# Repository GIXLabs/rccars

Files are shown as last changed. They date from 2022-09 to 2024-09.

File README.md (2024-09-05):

# Purpose

The following tutorial will get you up and running to build an RC car with the provided materials. All of the soldering is already done and the most of the code is flashed onto the brain board. It will be your responsibility to use the tools provided to you in your orientation bag along with the tools available in the Prototyping Lab to design and build a chassis for your car.

### Bill of Materials



# Electronics Assembly

1. Collect the above components from the Prototyping Lab staff.

1. Attach the components to the individual boards. AAA battery pack to brain board (only goes in one way). Bluetooth module to Bluetooth board (RCA, not RCM). Motors to motor board (needs a screwdriver and wires may need to be switched later).

    Component assembly

1. Stack the boards together with the brain at the bottom and Bluetooth at the top. Make sure to align them properly (see image).

    Full assembly

1. Try placing 3 AAA batteries in their holder and turn it on. If you've assembled everything correctly, the blue and red lights on the underside of the Bluetooth module should start blinking.

# Flashing Code

1. The code for the brain board is written in CircuitPython, which means you will not need to download any software to edit and manipulate the code. 
1. Download the RC Car code from [here](src/python/code.py). Make sure it is named `code.py`.

    Image of the button to click

1. Using a micro USB cable, connect the brain board to your computer (you do not need to disconnect the other boards). Your computer should now have a new USB drive available named `CIRCUITPY` where the code is stored.
1. Click and drag `code.py` onto `CIRCUITPY`, replacing the file that is on the drive.
1. Your code should now be running on the brain board. If you would like to edit this code, just open `code.py` in any text editor (TextEdit and NotePad are fine). The new code will run whenever you save.
    1. Editing code this way does not give you access to any debugging outputs, so you may want to edit using [Mu](https://codewith.mu/en/download) or [Thonny](https://thonny.org/) so you can read any `print()` statements you add to the code.
    1. The max speed of the default code is slow, which you may want to change if you want to win the race.
    1. Python uses spacing in a particular way, so you may need to match the indendation of lines.
    1. For more details on how the code works see [here.](src/README.md)

# Connecting via Remote
1. Place the Bluetooth module marked `RCM` in the remote. It should only fit one way.

1. Plug in the 9V batteries on both your remote and turn on the AAA batteries on your car.

1. The lights on the Bluetooth dongles (HC-05) will stop blinking when they have successfully paired.

1. If it fails to pair, try power cycling the car ands the remote.

# Make your Chassis
1. Design and build the body of the RC car, you are welcome to use the materials provided in the Prototyping Lab from cardboard to wood. Make sure it holds everything! We've produced a tutorial if you'd like to start with a lasered template [here](lasering.md).

1. Attach the gear motors to the body of the RC car that you have designed/built and assemble the tires. Depending on how you attach the motors, you may have to change some wires to get it to move forward (instructions below).

# Debugging Motors
If you have been able to connect to your RC car, but it is going the wrong direction, you may need to swap the motor wires.
- If your car is going backward when it should be going forward - Swap the red and black wires on both motors.
- If your car is going left when it should be going right or right when it should be going left - Swap which side of the motor driver your motors are wired to.
- For other problems, ask a member of the Prototyping Lab staff.

### Congratulations you are now connected to the RC car! Happy racing! 🏁🏎

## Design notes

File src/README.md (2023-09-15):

# Theory of Operation
The RC Car consists of two parts:
- The car, which runs on CircuitPython
- The remote, which runs on C

They communicate through two paired Bluetooth dongles (HC-05), with the remote acting as a sender and car acting as a receiver. We expect you will want to edit the car code, but don't recommend editing the remote code.

The remote code first sets up each pin, then goes into an infinite loop. Each time through the loop, the code looks for which button is pressed and sends the corresponding command over the Bluetooth connection. When no button is pressed the remote sends the "stop" command ('S').

The car code first setups up each pin appropriately as either input or output, then goes into an infinite loop. Each time through the loop, the code checks for a command from the remote. When a command is received, a series of `if` and `elif` statements check to see what command was sent and tells the motors what to do accordingly.

The car controls direction via a scheme called tank steering. Instead of having a wheel that turns at the front to determine direction, like in a car, the two wheels move in different directions depending on which way you would like to turn. For example, a right turn involves spinning the left wheel forward and the right wheel backwards. While this allows for a tighter turning radius, it makes smooth turns rather challenging. This steering scheme was chosen for the ease of assembly and simplicity of the code.

# Commands

Image of controller with buttons

| Command | Action |
| --- | ---|
| F | Turn both motors on moving forward. |
| L | Turn left by spinning the right motor forward and the left motor backwards |
| R | Turn right by spinning the left motor forward and the right motor backwards |
| B | Go backwards by spinning both motors backward |
| S | Stop both motors (note: there is no button associated with this on the remote) |
| Q | Currently does nothing, but could be programmed on the car to do whatever you would like |
| N | Boost by turning up the speed to the maximum for 2 seconds. 10 second cooldown |

# Boost
The boost is the most confusing part of the code. It works by first detecting that the 'N' character was sent.
1. Check whether enough time has elapsed since the last boost. Default cooldown is 10 seconds.
    1. Set the motor speed to the maximum value.
        1. Setting the speed impacts all motion of the car. For example, the left and right turns will also go at whatever you most recently set the speed to.
    1. Set the car to move forward and wait for 2 seconds so it moves forward at maximum speed for 2 seconds.
    1. Set the speed back to the default (slower) speed.
    1. Reset the Bluetooth buffer to clear extra commands from the remote that may have come in during the boost (don't delete this, but don't feel like you have to understand it either).
    1. Save the time you last boosted so the cooldown can take effect.

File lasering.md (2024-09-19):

# Important laser rules
1. **DON'T WALK AWAY FROM A RUNNING LASER** - every makerspace eventually burns down due to lasers. We suggest bringing a stool and your computer with you. Unattended cuts will be interrupted and the user may have their access revoked.
1. Only use approved materials - materials already in the Lab are pre-approved, but you will need to check with Prototyping Lab staff if you want to cut or engrave something else.

# Making a basic laser chassis (no design experience needed)

1. Choose from one of the templates made by our staff, downloading the file as an svg.
    1. Formula E by Aayush Kumar (Cohort 7). [SVG here.](/CAD/svg/RC_Car_Formula-E/RC_Car_Formula-E_layout.svg)
    
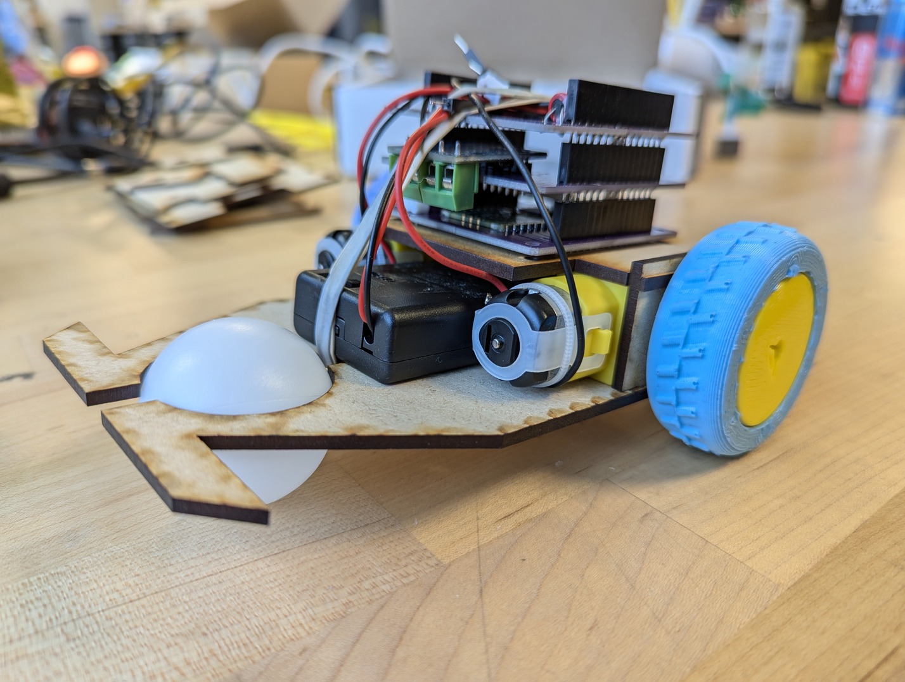
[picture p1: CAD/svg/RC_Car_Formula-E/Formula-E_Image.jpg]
Formula-E car image
    

    1. Van by Liliana Hsu (Cohort 7). [SVG here.](/CAD/svg/RC_Car_Van/RC_Car_Van_layout.svg)
    
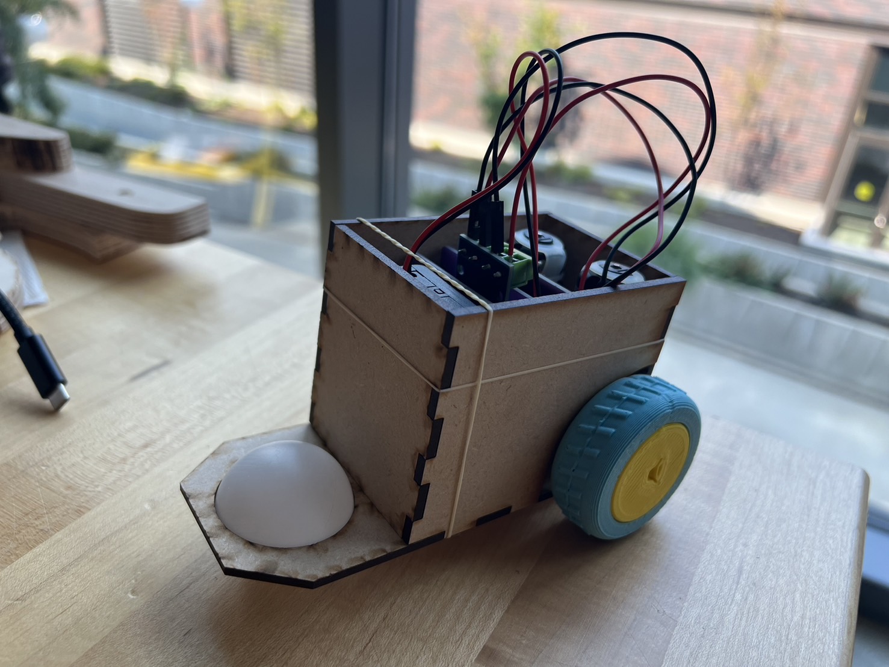
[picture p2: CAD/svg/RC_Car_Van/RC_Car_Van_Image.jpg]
Van car image
    

    1. Batperson car by Kevin Arne. [SVG here.](/CAD/svg/RC_Car_Batperson/base_template.svg)
    
    Batperson car image
1. Ask a member of staff to invite you to the Glowforge system. You will need to sign up for an account, but it is free. Please skip any features that ask for a credit card.
    1. You will get an email and you'll need to click "Click here to get started." Feel free to skip the tutorials.
1. "Create a new design" and "Upload a file" in the [Glowforge interface](https://app.glowforge.com)

    Image of Glowforge home screen

1. Find the 1/8" MDF in the laser material storage and put a sheet of it in your laser on the black honeycomb tray. Position doesn't matter much, and you can close the lid once you have the piece in. If you can, try to use pieces that already have something cut out of them. The numbers in the top right of the Glowforge interface indicate which laser is yours. The number on the machine is near the barcode.
1. You will need to set the material to "Medium Draftboard" in the top left of the Glowforge interface. You may have to search using the search box.

    Image showing where to select materials
    
    1. Greyed out parts are ones outside the Glowforge's cuttable area and will need to be moved onto the material.

1. Add any additional features you might want. [Here is a file with some pieces you can scale and move around in the Glowforge interface.](/CAD/svg) There is a download symbol on each of these pages that you'll need to use.

    Image of Glowforge interface

1. In the Glowforge interface, click and drag those pieces around on the generated box pieces to place them where you want them. Be careful not to accidentally scale the pieces from the template, but the other pieces can be scaled to your liking.

1. Set the text to "Ignore."

    Image showing where Ignore is found

1. Make sure that all of your parts are on the material in the laser and are not greyed out. You can box select groups of them and move them around.
    1. If you are using scraps, you can move items you don't want to cut outside the cuttable area. Anything greyed out won't be cut, which is sometimes desirable.
1. Click "Print" in the top right of the interface.

    Image showing the Print button

1. Press the big glowing button on the Glowforge and stay to watch your cut. Watching your cut is important as fires are common in lasers.
1. Once the laser has stopped making noise, you can open the lid and pull the parts out (don't worry, they aren't hot).
1. You've made your first box! Test it out and iterate!

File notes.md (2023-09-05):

- 4 io lines are needed to power the motor driver.
- A pair of UART lines are needed for Bluetooth.
- Swap 9V battery on main board for AAA connected with JST PH 2.0

# Nano Pin Mappings
The RC form factor is numbered starting with pin 1 in the top left and going clockwise. The view is from the Nano side with the rounded corner in the top left.

| RC Form Factor | Nano Pin | Current Use | Proposed Mapping on Pico |
| --- | --- | --- | --- |
| 1 | D13 | | GP13 |
| 2 | 3V3 | | 3v3(OUT) |
| 3 | REF | | ADC_VREF |
| 4 | A0 | | ADC0 |
| 5 | A1 | | ADC1 |
| 6 | A2 | | ADC2 |
| 7 | A3 | | GP2 |
| 8 | A4 | SDA(not used, but should be replicated) | GP20 |
| 9 | A5 | SCL(not used, but should be replicated) | GP21 |
| 10 | A6 | | GP3 |
| 11 | A7 | | GP 14 |
| 12 | 5V | Used by Bluetooth board for power | VSYS |
| 13 | RST | | RUN |
| 14 | GND | Used by motor board for ground | |
| 15 | VIN | Power in, currently 9V, used by motor board for power | VSYS |
| --- | --- | --- | |
| 16 | TX1 | | GP1 |
| 17 | RX0 | | GP0 |
| 18 | RST | | GP15 |
| 19 | GND | | GND |
| 20 | D2 | Goes into RXD on Bluetooth | GP16 |
| 21 | D3 | Goes into TXD on Bluetooth | GP17 |
| 22 | D4 | | GP4 |
| 23 | D5 | A-1B on motor board | GP5 |
| 24 | D6 | A-1A on motor board | GP6 |
| 25 | D7 | | GP7 |
| 26 | D8 | | GP8 |
| 27 | D9 | | GP9 |
| 28 | D10 | B-2A (B-1B) on motor board | GP10 |
| 29 | D11 | B-1A on motor board | GP 11 |
| 30 | D12 | | GP12 |

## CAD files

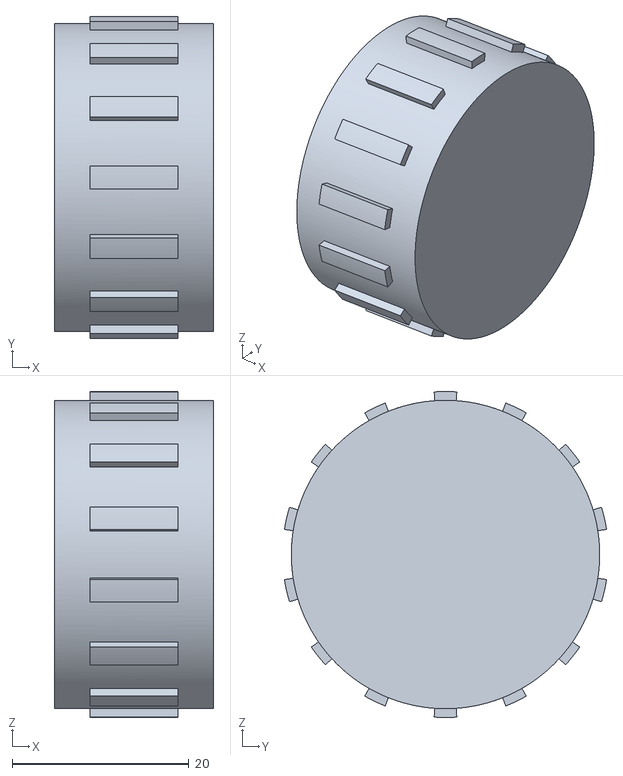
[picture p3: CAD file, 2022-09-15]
CAD/tire_mold/TyreMotorMount.stl
18.0 x 36.5 x 36.9

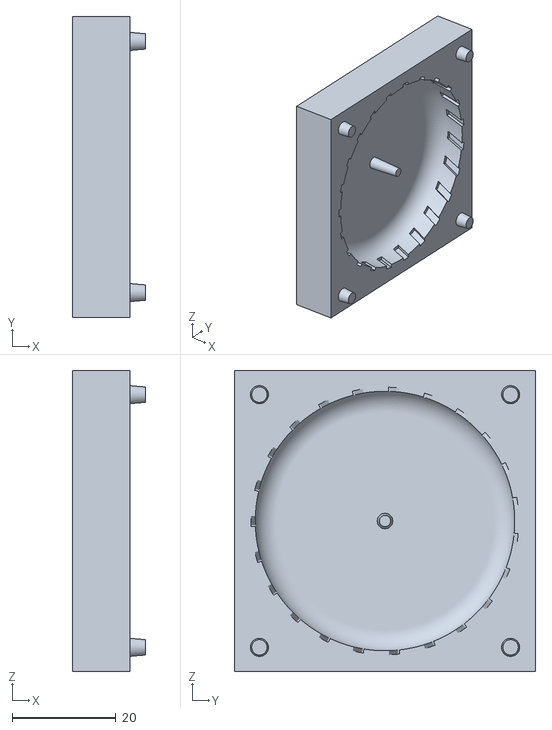
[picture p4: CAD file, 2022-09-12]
CAD/tire_mold/MoldBottom.stl
14.0 x 58.0 x 58.0

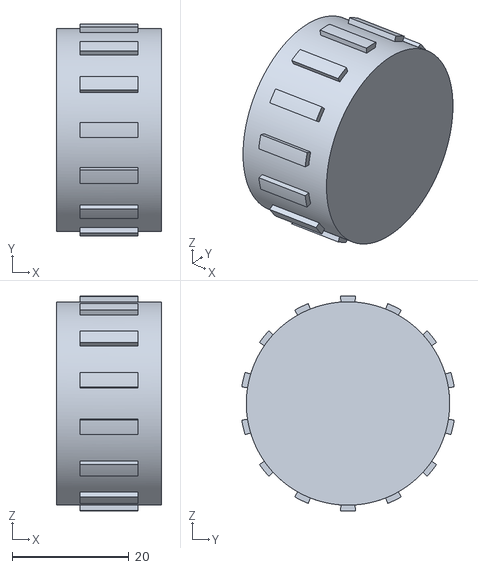
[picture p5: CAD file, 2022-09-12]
CAD/tire_mold/MoldInternal.stl
18.0 x 36.5 x 36.9

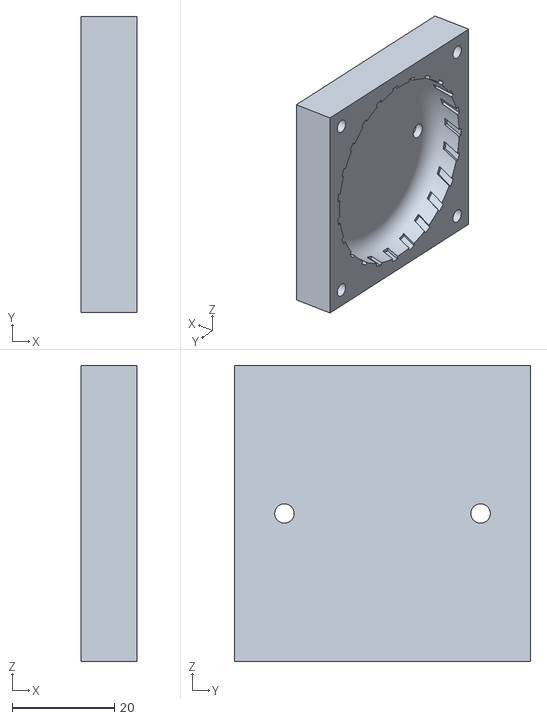
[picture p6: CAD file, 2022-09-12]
CAD/tire_mold/MoldTop.stl
11.0 x 58.0 x 58.0

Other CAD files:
CAD/svg/RC_Car_Formula-E/RC_Car_Formula-E.f3d
CAD/svg/RC_Car_Van/RC_Car_Van.f3d
CAD/tire_mold/silicone_mold_tyres.f3d

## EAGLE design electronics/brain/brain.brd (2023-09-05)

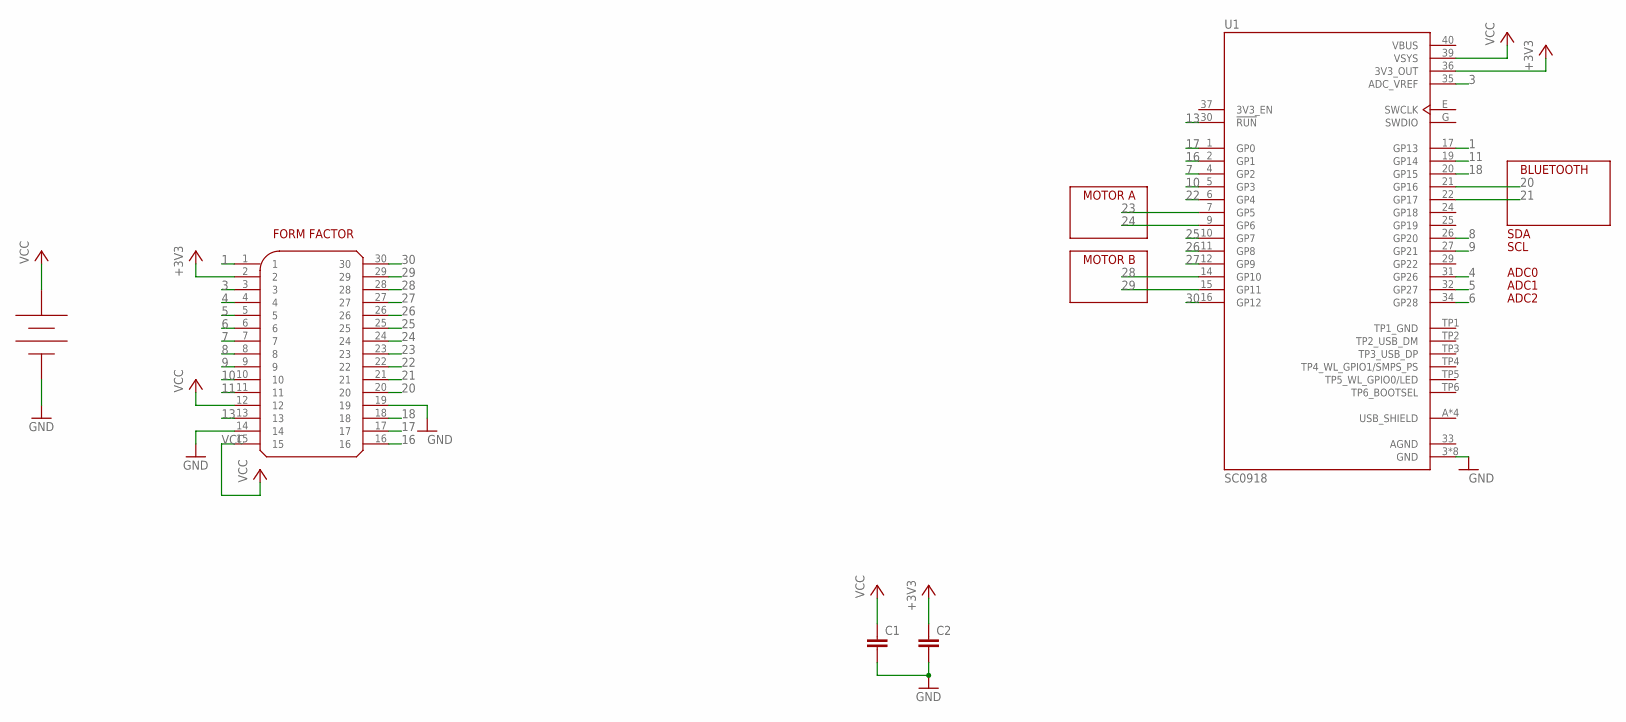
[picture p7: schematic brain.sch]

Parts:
C1, C2: C-EU050-025X075; C050-025X075
U1: SC0918; MODULE_SC0918
U$4: RC_FORM_FACTOR
U$6: LIPO_BATTERY; JST_PH

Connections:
1: U1.17 (GP13), U$4.1
3: U1.35 (ADC_VREF), U$4.3
4: U1.31 (GP26), U$4.4
5: U1.32 (GP27), U$4.5
6: U1.34 (GP28), U$4.6
7: U1.4 (GP2), U$4.7
8: U1.26 (GP20), U$4.8
9: U1.27 (GP21), U$4.9
10: U1.5 (GP3), U$4.10
11: U1.19 (GP14), U$4.11
13: U1.30 (!RUN), U$4.13
16: U1.2 (GP1), U$4.16
17: U1.1 (GP0), U$4.17
18: U1.20 (GP15), U$4.18
20: U1.21 (GP16), U$4.20
21: U1.22 (GP17), U$4.21
22: U1.6 (GP4), U$4.22
23: U1.7 (GP5), U$4.23
24: U1.9 (GP6), U$4.24
25: U1.10 (GP7), U$4.25
26: U1.11 (GP8), U$4.26
27: U1.12 (GP9), U$4.27
28: U1.14 (GP10), U$4.28
29: U1.15 (GP11), U$4.29
30: U1.16 (GP12), U$4.30
+3V3: C2.1, U1.36 (3V3_OUT), U$4.2
AGND: U1.33 (AGND)
GND: C1.2, C2.2, U1.3 (GND), U1.8 (GND), U1.13 (GND), U1.18 (GND), U1.23 (GND), U1.28 (GND), U1.38 (GND), U1.F (GND), U$4.14, U$4.19, U$6.GND (NEG)
TP1_GND: U1.TP1 (TP1_GND)
USB_SHIELD: U1.A (USB_SHIELD), U1.B (USB_SHIELD), U1.C (USB_SHIELD), U1.D (USB_SHIELD)
VBUS: U1.40 (VBUS)
VCC: C1.1, U1.39 (VSYS), U$4.12, U$4.15, U$6.POS

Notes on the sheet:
FORM FACTOR
ADC0
ADC1
ADC2
MOTOR A
MOTOR B
BLUETOOTH
SDA
SCL

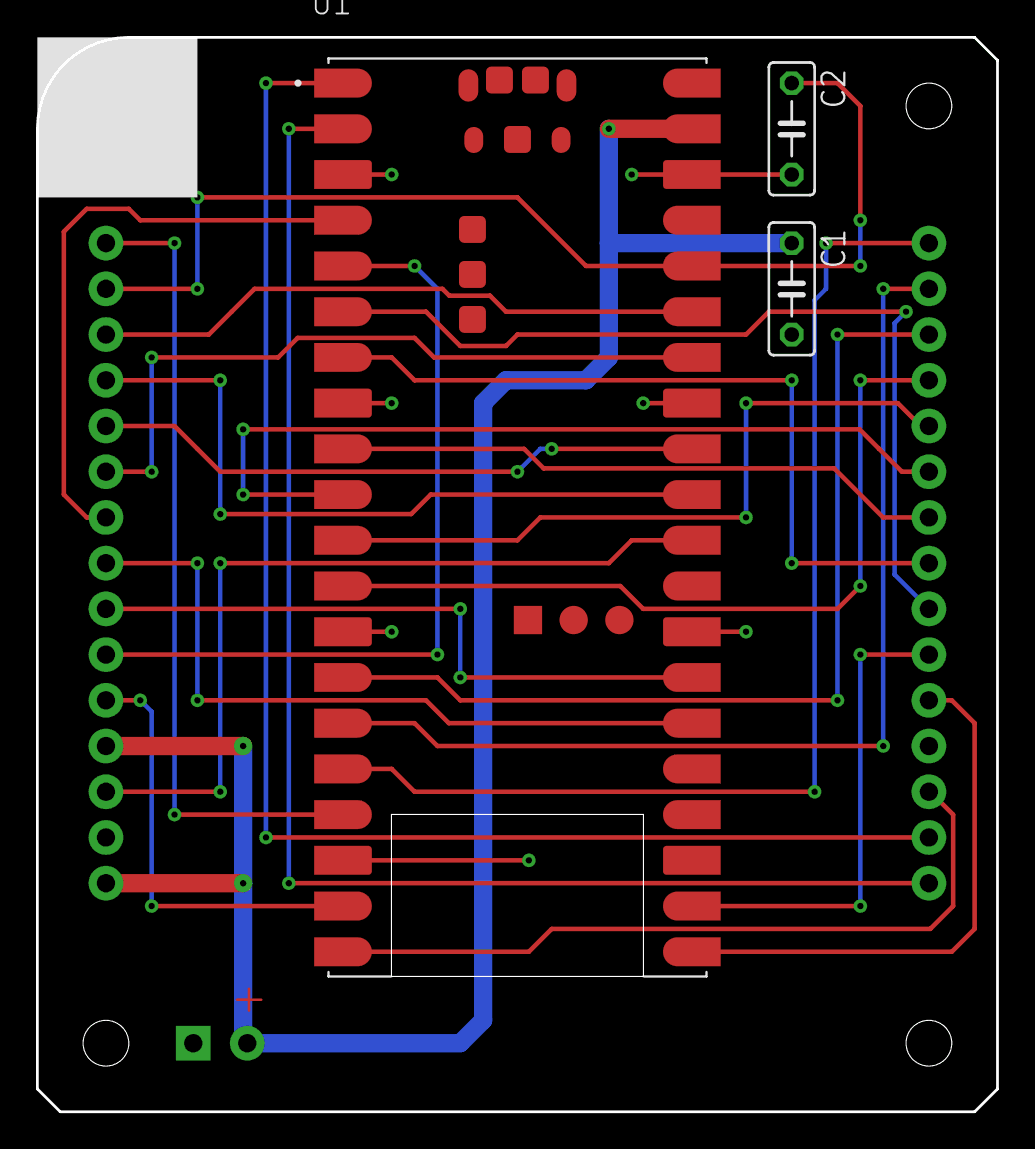
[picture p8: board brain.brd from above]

Board: 2 copper layers, 53.3 x 59.7 mm, 5 parts (0 on the bottom side), 29 nets.

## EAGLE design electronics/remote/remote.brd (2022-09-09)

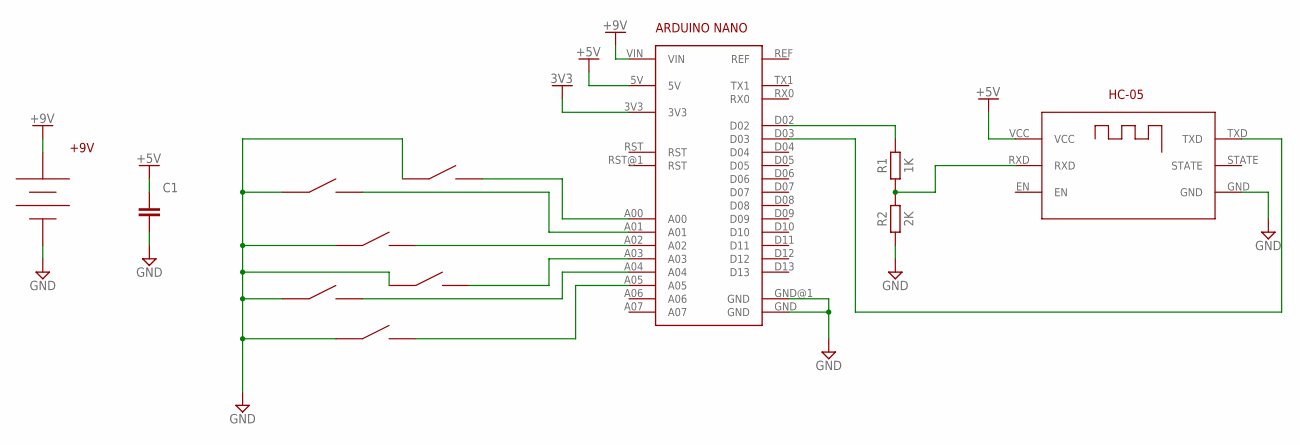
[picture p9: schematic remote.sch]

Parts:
C1: C_RADIAL-12.5MM-DIA; CAPRD550W60D1025H1250B
DOWN: TACT_SWITCH_6MM
LEFT: TACT_SWITCH_6MM
LEFT_BUMPER: TACT_SWITCH_6MM
R1: 1K; RESAD1176W63L850D250B
R2: 2K; RESAD1176W63L850D250B
RIGHT: TACT_SWITCH_6MM
RIGHT_BUMPER: TACT_SWITCH_6MM
U$1: 9V_BATTERY
U$2: HC-05
U$9: ARDUINO-NANO-V3
UP: TACT_SWITCH_6MM

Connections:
3V3: U$9.3V3
+5V: C1.1, U$2.VCC, U$9.5V
+9V: U$1.POS (9V), U$9.VIN
GND: C1.2, DOWN.A1 (A), DOWN.A2 (A), LEFT.A1 (A), LEFT.A2 (A), LEFT_BUMPER.A1 (A), LEFT_BUMPER.A2 (A), R2.1, RIGHT.A1 (A), RIGHT.A2 (A), RIGHT_BUMPER.A1 (A), RIGHT_BUMPER.A2 (A), U$1.NEG, U$2.GND, U$9.GND, U$9.GND@1 (GND), UP.A1 (A), UP.A2 (A)
unnamed: R1.2, U$9.D02
unnamed: RIGHT_BUMPER.B1 (B), RIGHT_BUMPER.B2 (B), U$9.A00
unnamed: LEFT_BUMPER.B1 (B), LEFT_BUMPER.B2 (B), U$9.A01
unnamed: U$9.A02, UP.B1 (B), UP.B2 (B)
unnamed: RIGHT.B1 (B), RIGHT.B2 (B), U$9.A03
unnamed: LEFT.B1 (B), LEFT.B2 (B), U$9.A04
unnamed: DOWN.B1 (B), DOWN.B2 (B), U$9.A05
unnamed: R1.1, R2.2, U$2.RXD
unnamed: U$2.TXD, U$9.D03

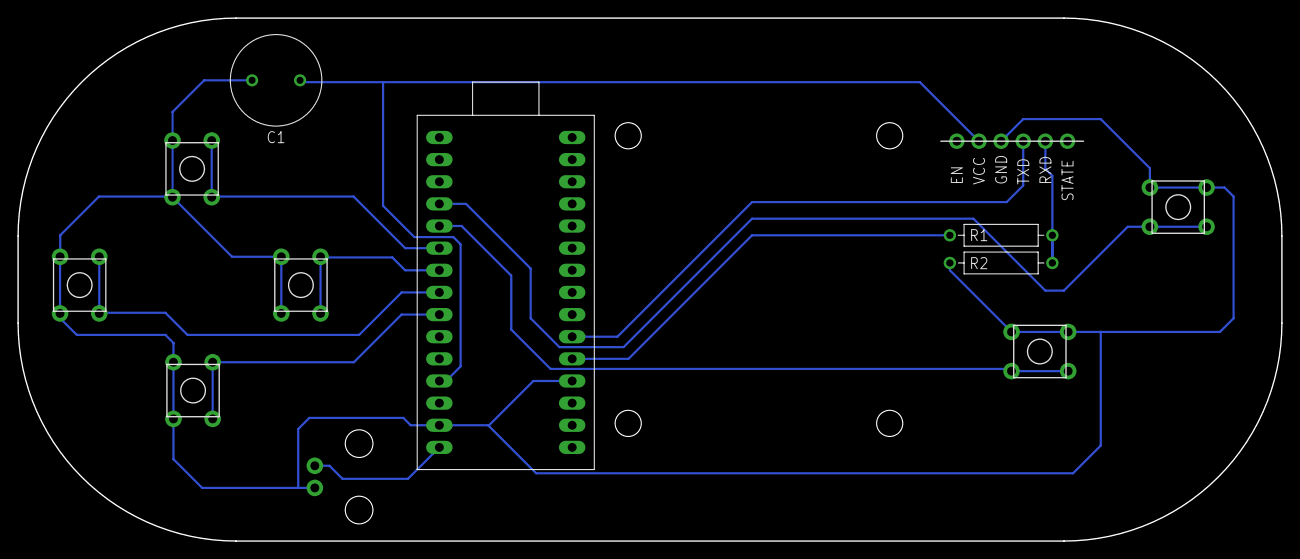
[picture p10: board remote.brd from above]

Board: 2 copper layers, 145.0 x 60.0 mm, 12 parts (1 on the bottom side), 12 nets.

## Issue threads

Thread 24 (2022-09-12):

Add motor troubleshooting to the tutorial

kevinarne, 2022-09-12:

chuanisawesome, 2022-09-12:
added the troubleshooting for the motor but unsure if I am missing another troubleshooting step @kevinarne

Closed 2022-09-15.

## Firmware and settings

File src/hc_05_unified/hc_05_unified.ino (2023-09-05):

#include <SoftwareSerial.h>

#define BT_MASTER   "RCM_29"
#define BT_APPREN   "RCA_29"
String APPREN_ADDRESS;

SoftwareSerial apprenSerial(5, 4); // RX, TX
SoftwareSerial masterSerial(7, 6);

const byte numChars = 50;
char receivedChars[numChars];
boolean newData = false;

void setup() {
  Serial.begin(38400);

  apprenSerial.begin(38400);
  Serial.println("Arduino receiver");
  apprenSerial.print("AT+ROLE=0\r\n");
  delay(100);  
  apprenSerial.print("AT+ADDR?\r\n");
  delay(100);
  apprenSerial.print("AT+NAME="+String(BT_APPREN)+"\r\n");
  delay(100);
  apprenSerial.print("AT+UART=38400,0,0\r\n");
  delay(1500);
  recvWithStartEndMarkers();
  Serial.println("1");
  showNewData();
  Serial.println("2");
  parseData();  
  Serial.println("3");


  // Master
  masterSerial.begin(38400);
  Serial.println("Master");
  masterSerial.print("AT+ROLE=1\r\n");
  delay(100);  
  masterSerial.print("AT+NAME="+String(BT_MASTER)+"\r\n");
  delay(100);
  masterSerial.print("AT+BIND="+String(APPREN_ADDRESS)+"\r\n");
  delay(100);
  masterSerial.print("AT+UART=38400,0,0\r\n");
  delay(200);
  Serial.println("Devices flashed with new names successfully.");
}

void loop() {
  if (apprenSerial.available())
    Serial.write(apprenSerial.read());
  // if (Serial.available())
  //   apprenSerial.write(Serial.read());

    // master 
  // if (masterSerial.available())
  //   Serial.write(masterSerial.read());
  // if (Serial.available())
  //   masterSerial.write(Serial.read());
}

void recvWithStartEndMarkers() {
    static boolean recvInProgress = false;
    static byte ndx = 0;
    char startMarker = '+';
    char endMarker = '\n';
    char rc;
    while (apprenSerial.available() > 0 && newData == false) {
        rc = apprenSerial.read();

        if (recvInProgress == true) {
            if (rc != endMarker) {
                receivedChars[ndx] = rc;
                ndx++;
                if (ndx >= numChars) {
                    ndx = numChars - 1;
                }
            }
            else {
                receivedChars[ndx] = '\0'; // terminate the string
                recvInProgress = false;
                ndx = 0;
                newData = true;
            }
        }
        else if (rc == startMarker) {
            recvInProgress = true;
        }
    }
}

void showNewData() {
    if (newData == true) {
        Serial.println(receivedChars);
        newData = false;
    }
}

void parseData(){
  for (byte i = 0; i <= strlen(receivedChars); i++)
  {
    if (receivedChars[i] == ':')
    receivedChars[i] = ',' ;
  }
  Serial.println(&receivedChars[5]);//print from from after first ':' to end
  APPREN_ADDRESS = &receivedChars[5];
}

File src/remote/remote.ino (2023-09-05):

#include <SoftwareSerial.h>
SoftwareSerial BTserial(3, 2); 

#define UP A2
#define LEFT A4
#define DOWN A5
#define RIGHT A3
#define LBUMPER A1
#define RBUMPER A0

void setup() {
  pinMode(UP, INPUT_PULLUP);
  pinMode(LEFT, INPUT_PULLUP);
  pinMode(DOWN, INPUT_PULLUP);
  pinMode(RIGHT, INPUT_PULLUP);
  pinMode(LBUMPER, INPUT_PULLUP);
  pinMode(RBUMPER, INPUT_PULLUP);
  Serial.begin(9600);
  BTserial.begin(38400);
}

void loop() {
  if(!digitalRead(UP))
  {
    Serial.println("Up pressed");
    BTserial.print('F');
  }
  else if (!digitalRead(DOWN))
  {
    Serial.println("Down pressed");
    BTserial.print('B');
  }
  else if (!digitalRead(LEFT))
  {
    Serial.println("Left pressed");
    BTserial.print('L');  
  }
  else if (!digitalRead(RIGHT))
  {
    Serial.println("Right pressed");
    BTserial.print('R');  
  }
  else if (!digitalRead(LBUMPER))
  {
    Serial.println("Left bumper pressed");
    BTserial.print('N');  
  }
  else if (!digitalRead(RBUMPER))
  {
    Serial.println("Right bumper pressed");
    BTserial.print('Q');  
  }
  else
  {
    Serial.println("Stopping");
    BTserial.print('S');  
  }
  delay(30);
}

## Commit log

2022-06-24 arduino code and stl files added
    [Base_plate v2.stl, Component1.stl, RC_Car_batch.3mf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]
2022-06-24 comments for arduino app added, double and trile spaces removed
2022-07-05 new STL files
    [Base_plate v2.stl, Component1.stl, RC_Car_batch.3mf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]
2022-07-21 fusion tyre mold added
    [silicone mold tyres v0.f3d]
2022-08-04 renamed stuff added gitignore
    [Silicone_Tyre_Top.stl, Silicone_Tyre_base.stl, silicone_mold_tyres.f3d]
2022-08-09 added arduino code to help change hc05 module to command mode
2022-08-09 added documentation to switch to command mode
2022-08-16 Adding Garrett's files. Appears to be missing the Bluetooth board.
    [brain.brd, brain.sch, motor.brd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]
2022-08-17 Added chamfers and filet to brain board.
    [brain.brd]
2022-08-17 Added chamfers and filet to remaining boards.
    [motor.brd, power.brd]
2022-08-17 Added decoupling capacitors to brain board. Also adjusted the origin to be in the bottom left corner of the PCB.
    [brain.brd, brain.sch]
2022-08-17 Added mini USB notch on brain board to aid in placing Nano.
    [brain.brd]
2022-08-19 Moved all boards so their bottom left corners are at the origin.
    [motor.brd, power.brd]
2022-08-19 Fixed board lengths for motor and power boards.
    [motor.brd, power.brd]
2022-08-22 On brain board: Added holes for strain relief of power cables. Added silkscreen to indicate ground and different power pins on Nano. Added silkscreen denoting the board. Added silkscreen to mark posi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
    [brain.brd]
2022-08-23 Changed name of power board to bluetooth to reflect its new purpose.
    [bluetooth.brd, bluetooth.sch]
2022-08-26 Update RC_car_code.ino
    Swapped Motor B pins to simplify wire routing
2022-08-26 Updated Boards for New Configuration
    Bluetooth board has been rearranged to accommodate board slot-in
    Motor Control Board flipped to be in the right spot
    [bluetooth.brd, bluetooth.sch, motor.brd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]
2022-08-29 arduino code for master and apprentice
2022-08-30 update name
    [silicone_mold_tyres.f3d]
2022-08-30 update foldername
    [silicone_mold_tyres.f3d]
2022-08-30 Added breadboard board. This commit is going to production.
    [bluetooth.sch, brain.brd, brain.sch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]
2022-09-08 master apprentice single script initial commit
    [MoldBottom.stl, MoldInternal.stl, MoldTop.stl]
2022-09-09 Moved PCBs files into this repository. Old rccars_pcb is now deprecated.
    [bluetooth.brd, bluetooth.sch, brain.brd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]
2022-09-14 Removed duplicate board designs. Duplication due to Kevin's lack of communication.
    [bluetooth.brd, bluetooth.sch, brain.brd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]
2022-09-15 Simplified some of the language on the instructions. Added some motor debugging.
2022-09-15 added tyre motor mount.
    [TyreMotorMount.stl]
2022-09-15 Initial commit of remote code. Bumper buttons currently send forward character, but that should be changed to handle other characters.
2022-09-21 Added new graphics for bill of materials section.
2023-08-03 Added initial notes and motor test script for CircuitPython conversion
2023-08-03 Mapped out all of the pins to the form factor on the current Nano brain board. These will inform the pin mapping on the Pico.
2023-08-03 Added form factor part to library to make it easier to build new boards to stack.
    [brain.brd]
2023-08-04 Updated motor pins. Added Bluetooth test script.
2023-08-05 Fleshed out pin mapping. Routed new brain board.
    [brain.brd, brain.sch]
2023-08-07 This version was ordered.
    [brain.brd]
2023-08-15 Fixed power issue in current iteration of boards.
    [brain.brd, brain.sch]
2023-08-17 Added pwm to both motors.
2023-08-17 Added initial bit of main script, with framework for motor class.
2023-08-17 Added some Bluetooth connection with motors, just forward and stop. Still need all other directions.
2023-08-17 Code is working for all directions and could be used now. Still needs edits to add boost and improve editability. Shooting for less than 20 lines of code in the main document with motor and bluetooth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
2023-08-17 Removed fragment on border. Changed vias on VCC to same diameter as traces (40 mil).
    [brain.brd]
2023-08-17 Added different codes for the extra buttons.
2023-08-22 Split motor controls into a separte file. Added if statements for other inputs. Pseudocode for boost.
2023-08-22 Updated some of the tutorial content to reflect the change to CircuitPython.
2023-09-05 Moved chassis making to later in the instructions.
2023-09-15 Added button layout and theory of operation for code.
2023-09-22 Added link to svgs. Added line about attaching the Bluetooth to the remote.
2024-09-04 Started port of laser tutorial from input challenge.
2024-09-04 Copied over assets for lasering tutorial from InputChallenge.
2024-09-04 Updated links to assets in lasering tutorial.
2024-09-04 Added link to lasering tutorial in main README.
2024-09-04 Updated svg folder with new design folders
    [RC_Car_Formula-E.f3d]
2024-09-05 Added laser safety to lasering tutorial.
2024-09-05 Updated links to lasering tutorial. Fixed one instance of Labs vs Lab
2024-09-07 Add RC_Car_Van folder with files
    [RC_Car_Van.f3d]
2024-09-19 Updated links to templates in lasering document.
